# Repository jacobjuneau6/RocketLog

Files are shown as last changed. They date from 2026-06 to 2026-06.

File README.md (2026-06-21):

# RocketLog
RocketLog is a rocket altimeter designed to fit in the estes So Long rocket and provide attitude and altitude data on the rocket logging to redundant internal flash.
# Pictures
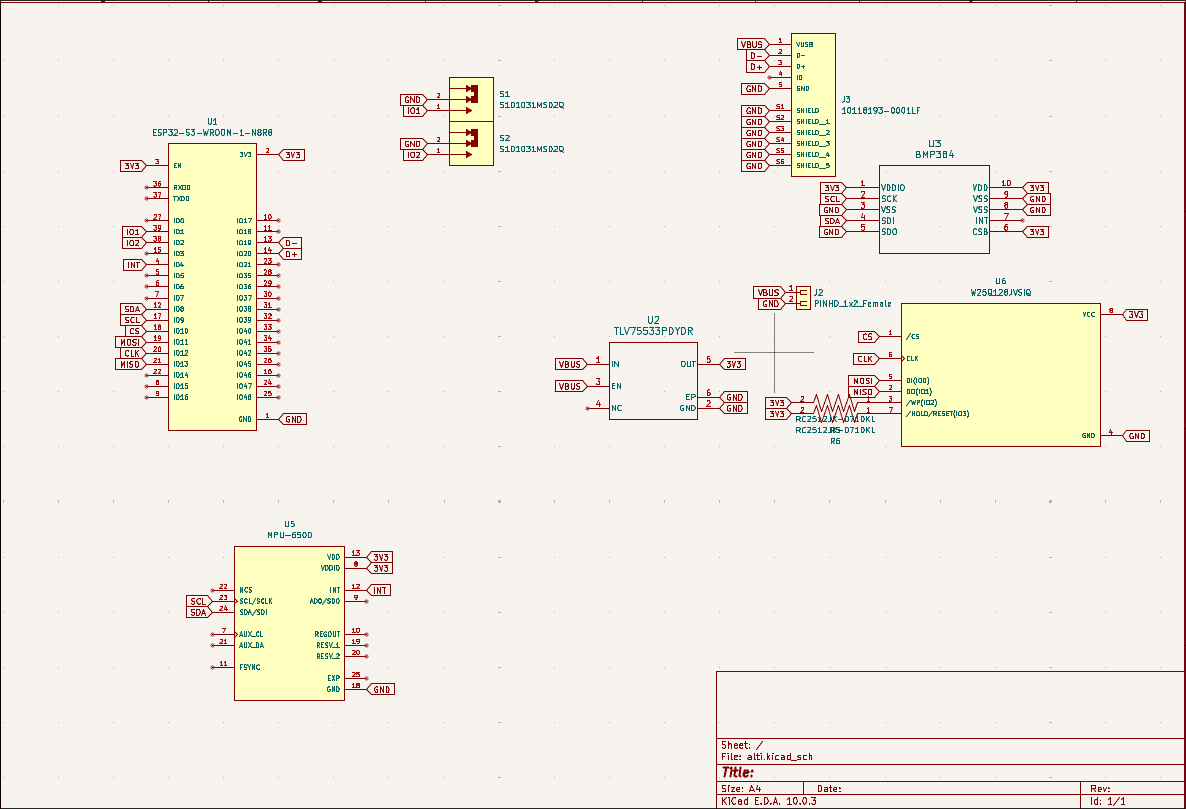
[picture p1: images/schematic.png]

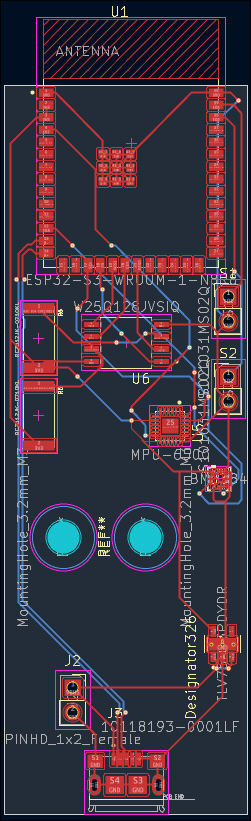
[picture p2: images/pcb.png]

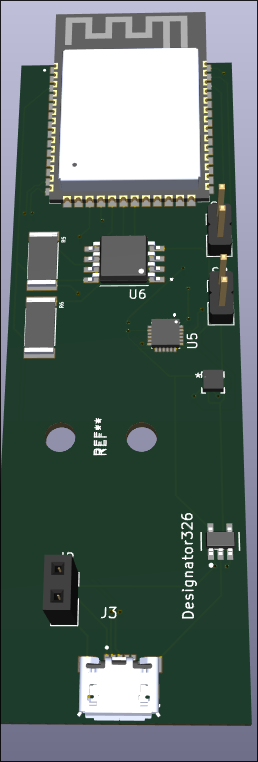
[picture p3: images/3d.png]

# Design
[![PCB Preview]()](https://kicanvas.org/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)Click the image to open the interactive KiCanvas viewer.
# Why
I have flown by custom painted and modified So Long rocket many times but have only been able to estimate the appogee and forces experienced. As I want to aluch sime more delicate payloads in the future, I want to see the forces that would be experienced by the payload before I fly some more delicate payloads.
# BOM
| Reference | Value | DigiKey_Part_Number | Link | Cost |
| --- | --- | --- | --- | --- |
| J3 | 10118193-0001LF | 609-4616-1-ND | [Link](https://www.digikey.com/en/products/detail/amphenol-cs-fci/10118193-0001LF/2785388) | $0.58 |
| R5,R6 | RC2512JK-0710KL | YAG3394CT-ND | [Link](https://www.digikey.com/en/products/detail/yageo/RC2512JK-0710KL/5922475) | $0.60 |
| U1 | ESP32-S3-WROOM-1-N8R8 | 5407-ESP32-S3-WROOM-1-N8R8CT-ND | [Link](https://www.digikey.com/en/products/detail/espressif-systems/ESP32-S3-WROOM-1-N8R8/15295891) | $6.73 |
| U2 | TLV75533PDYDR | 296-TLV75533PDYDRCT-ND | [Link](https://www.digikey.com/en/products/detail/texas-instruments/TLV75533PDYDR/22531567) | $0.30 |
| U3 | BMP384 | 828-BMP384CT-ND | [Link](https://www.digikey.com/en/products/detail/bosch-sensortec/BMP384/13681277) | $3.75 |
| U5 | MPU-6500 | 1428-1011-1-ND | [Link](https://www.digikey.com/en/products/detail/tdk-invensense/MPU-6500/4385412) | $8.00 |
| U6 | W25Q128JVSIQ | W25Q128JVSIQ-ND | [Flash](https://www.aliexpress.us/item/3256811354152848.html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) | $7.00 |
| PCB | Custom Boards & Stencils from JLCPCB | | | $27.00 |
| Battery | 300mAh battery | | [Battery](https://www.amazon.com/battery-Rechargeable-Lithium-Polymer-Connector/dp/B07BTTVX4Q?th=1) | $4.00 |
| Digikey Shipping | | | | $8.50 |

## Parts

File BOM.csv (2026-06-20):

Reference | Value | DigiKey_Part_Number
J3 | 10118193-0001LF | 609-4616-1-ND
R5,R6 | RC2512JK-0710KL | YAG3394CT-ND
U1 | ESP32-S3-WROOM-1-N8R8 | 5407-ESP32-S3-WROOM-1-N8R8CT-ND
U2 | TLV75533PDYDR | 296-TLV75533PDYDRCT-ND
U3 | BMP384 | 296-TLV75533PDYDRCT-ND
U5 | MPU-6500 | 1428-1011-1-ND
U6 | W25Q128JVSIQ | W25Q128JVSIQ-ND

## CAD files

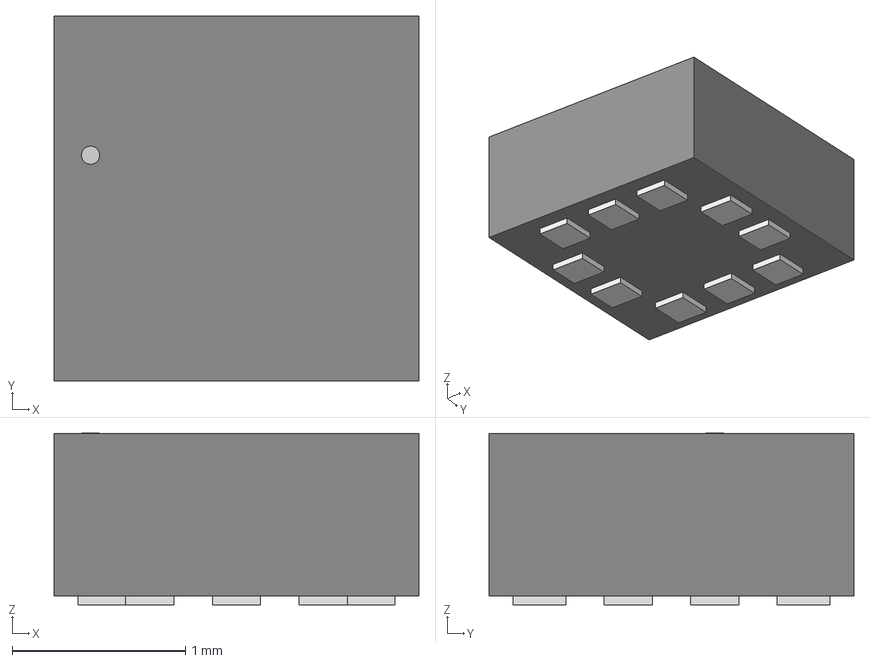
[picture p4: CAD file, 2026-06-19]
alti/symbols/BMP384/LGA10_2_0X2_0X0_95_BOS.step
2.11 x 2.11 x 0.993 mm

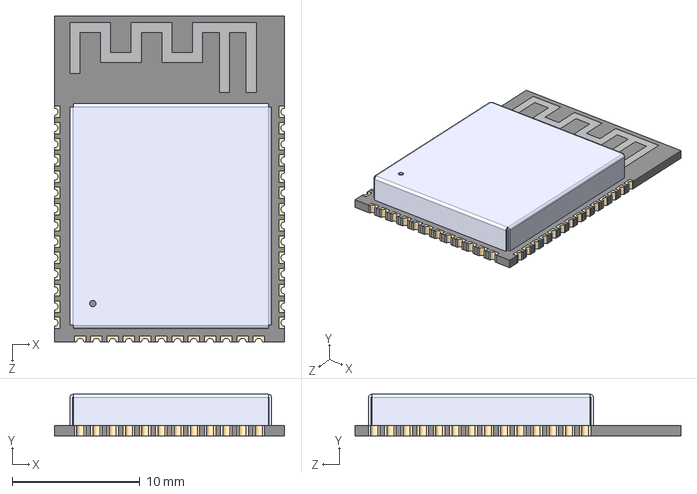
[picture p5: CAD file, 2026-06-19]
alti/symbols/ESP32-S3-WROOM-1-N8R8/ESP32-S3-WROOM-1-N8R8.step
18.0 x 3.25 x 25.5 mm

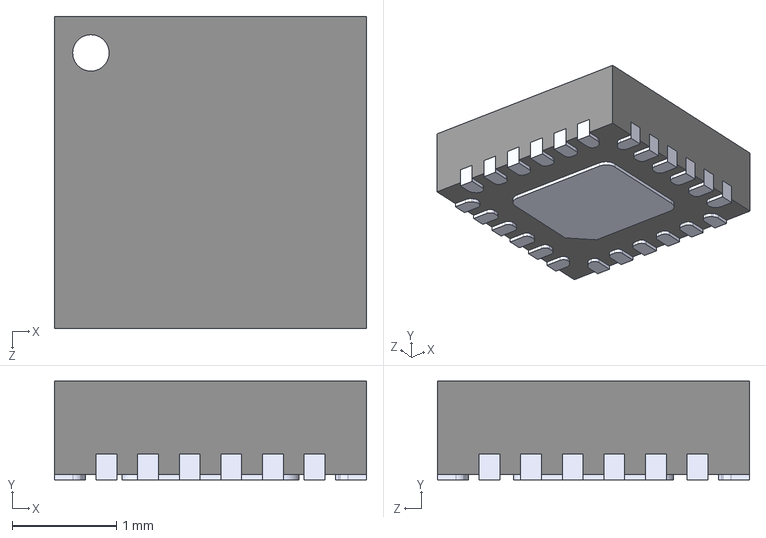
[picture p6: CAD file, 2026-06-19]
alti/symbols/MPU-6500/MPU-6500.step
3.00 x 0.95 x 3.00 mm

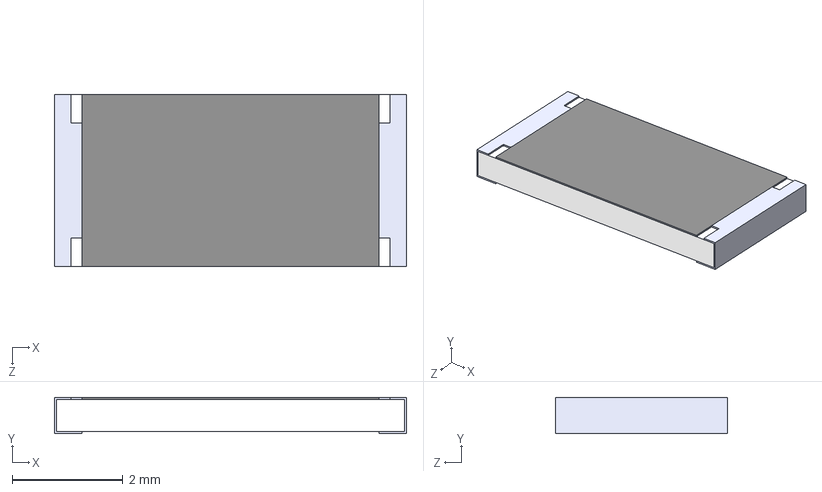
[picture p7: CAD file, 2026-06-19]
alti/symbols/RC2512JK-075K1L/RC2512JK-075K1L.step
6.35 x 0.65 x 3.10 mm

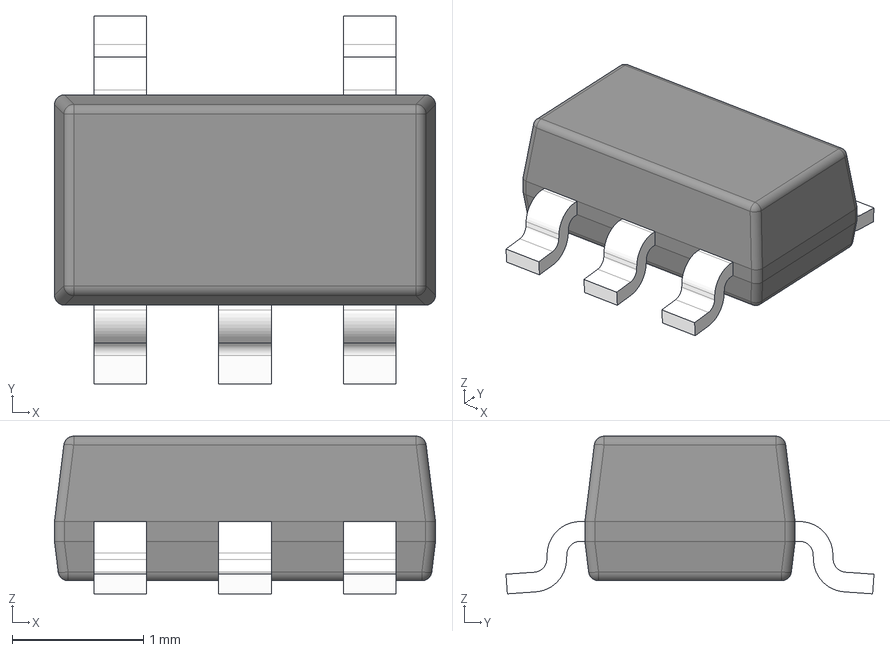
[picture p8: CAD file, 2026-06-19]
alti/symbols/ul_TLV75533PDYDR/DYD0005A.stp
2.90 x 2.80 x 1.20 mm
BODY-SOT
LEAD-SOT x 5
DIEPAD

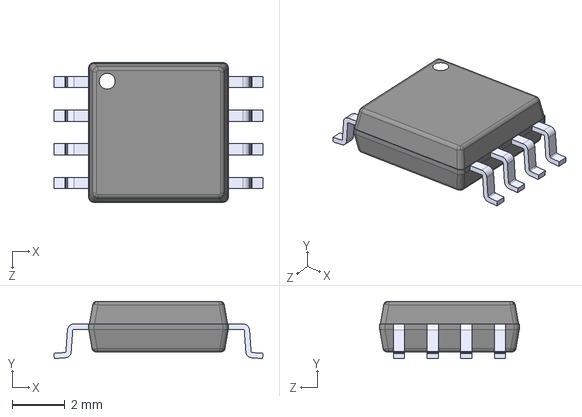
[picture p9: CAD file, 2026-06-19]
alti/symbols/W25Q128JVSIQ/W25Q128JVSIQ.step
7.90 x 2.16 x 5.28 mm

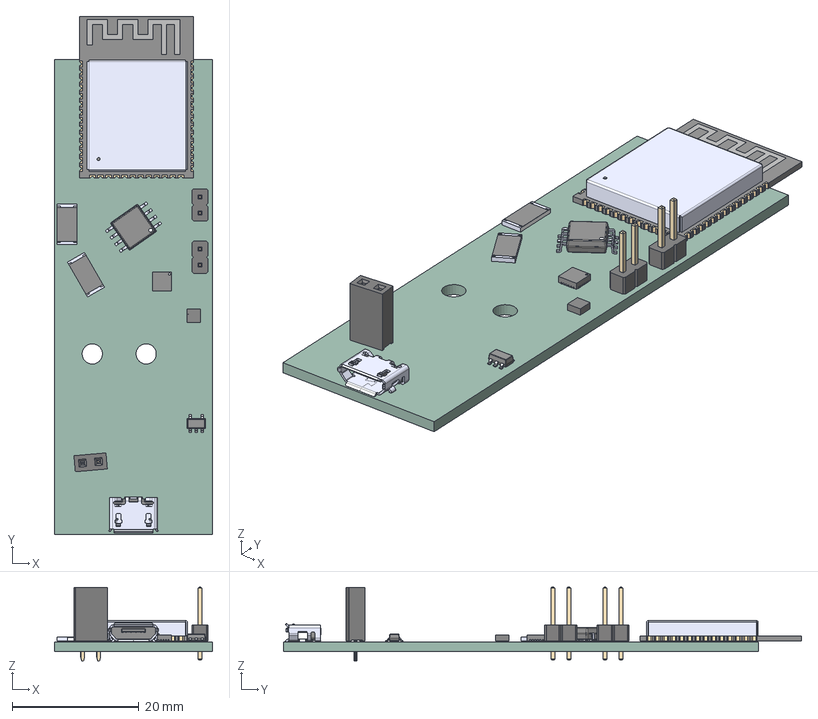
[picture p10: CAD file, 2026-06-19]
CAD/PCB.step
25.0 x 81.8 x 11.6 mm
W25Q32JWSSIQ
SR2512MK-071R1L x 2
PinHeader_1x02_P254mm_Vertical x 2
ESP32-S3-WROOM-1-N8R2
MPU-6500
10118193-0001LF
BODY-SOT
LEAD-SOT x 5
DIEPAD
PinSocket_1x02_P2.54mm_Vertical
alti_PCB

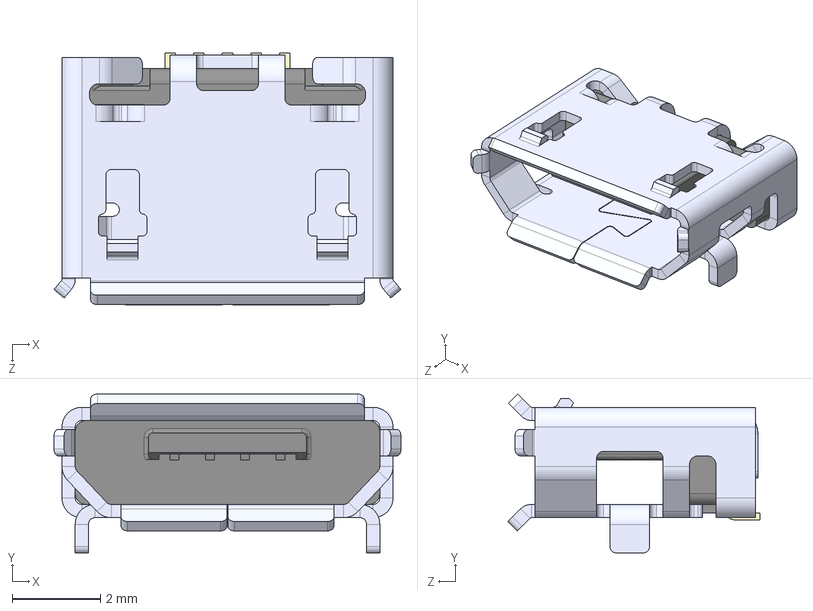
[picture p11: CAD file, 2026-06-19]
alti/symbols/10118193-0001LF--3DModel-STEP-56544.STEP
7.86 x 3.60 x 5.71 mm

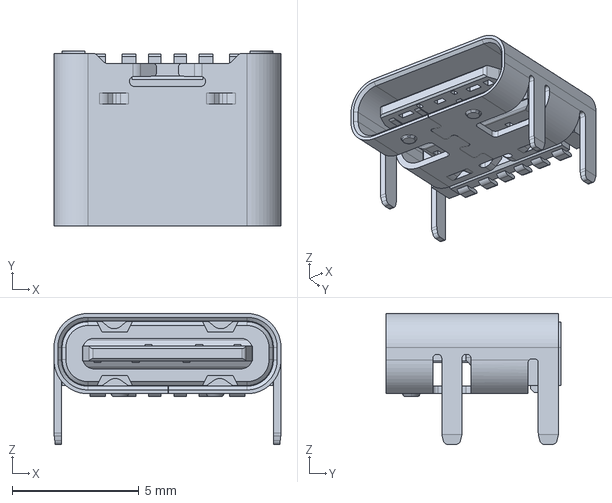
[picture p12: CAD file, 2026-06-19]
alti/symbols/2171750001/2171750001.stp
8.94 x 6.90 x 5.16 mm

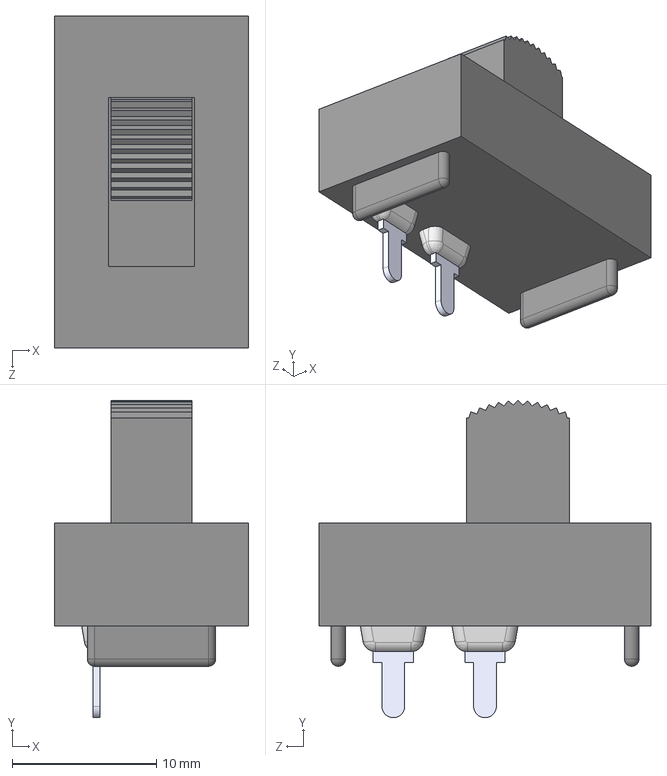
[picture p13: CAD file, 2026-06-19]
alti/symbols/S101031MS02Q/S101031MS02Q.step
13.5 x 22.0 x 23.0 mm

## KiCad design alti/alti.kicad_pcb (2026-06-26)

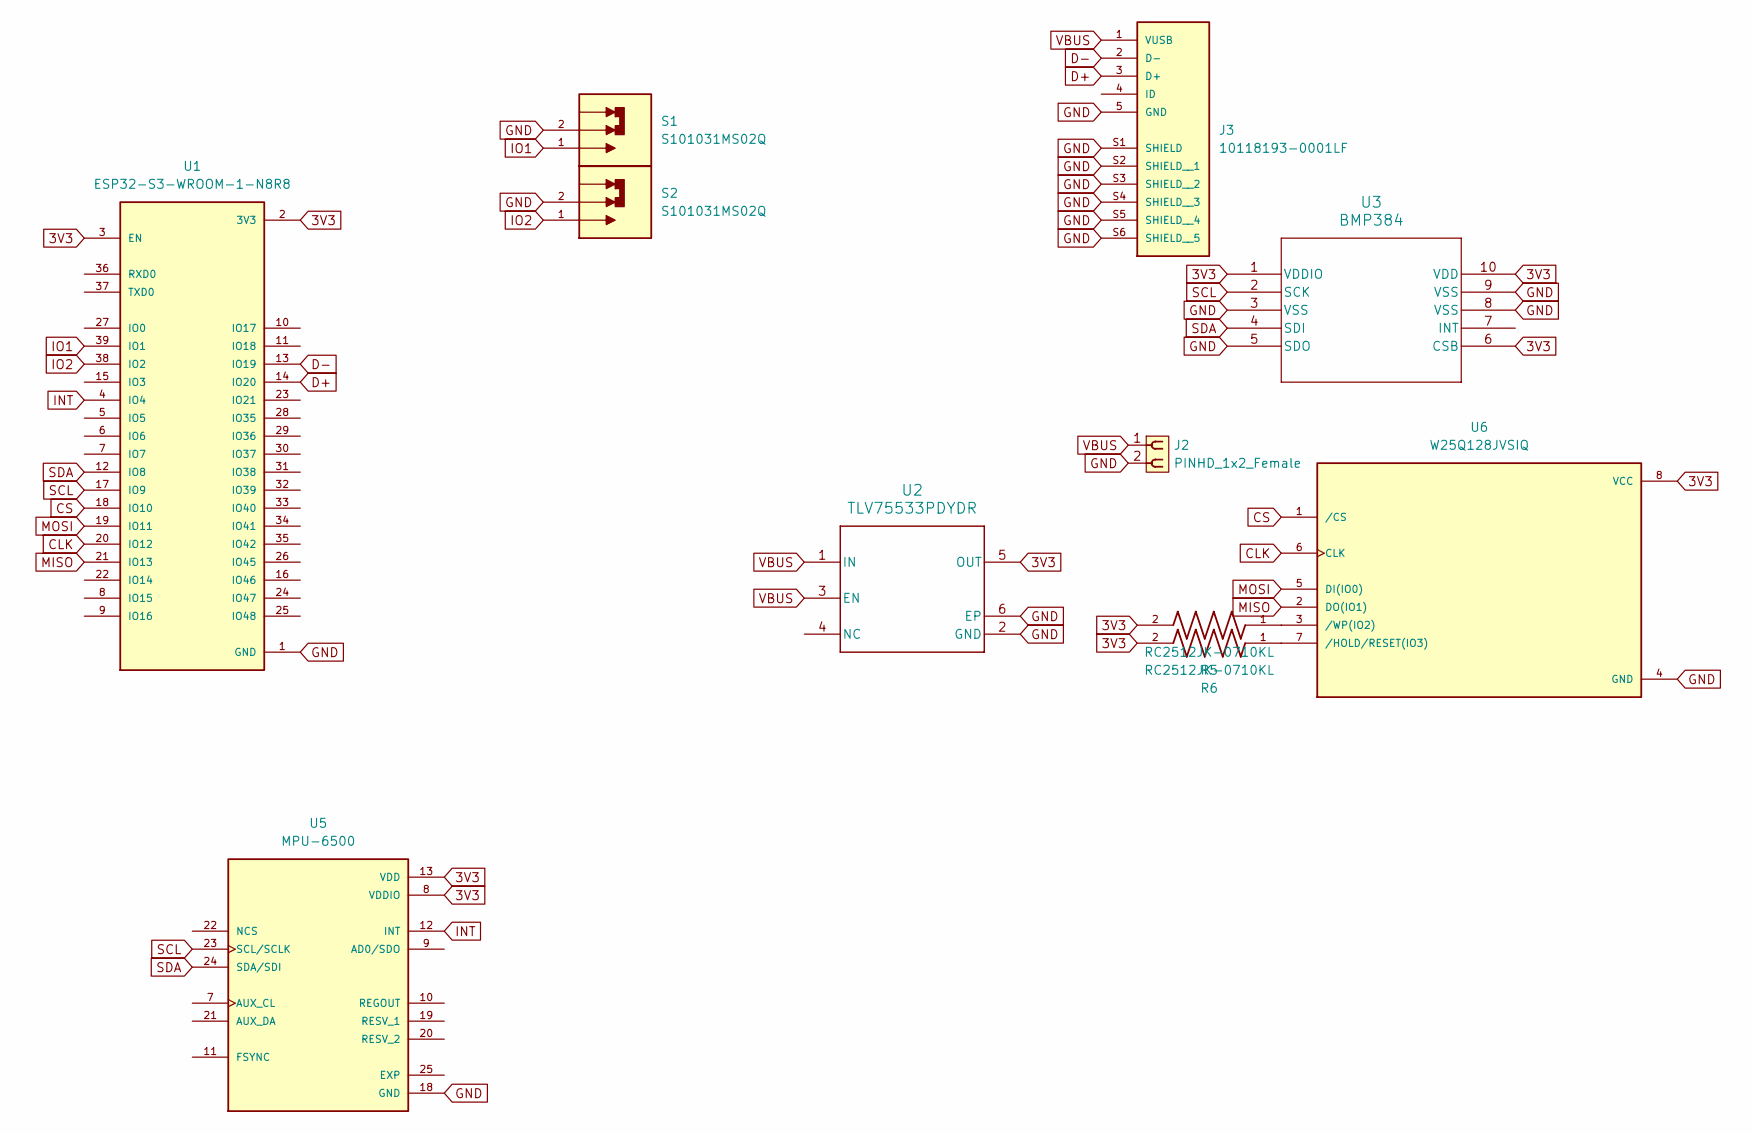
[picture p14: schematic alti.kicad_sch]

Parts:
J2: PINHD_1x2_Female; PinSocket_1x02_P2.54mm_Vertical
J3: 10118193-0001LF; AMPHENOL_10118193-0001LF; PARTREV E; DigiKey_Part_Number 609-4616-1-ND
R5, R6: RC2512JK-0710KL; RESC6331X65N; DigiKey_Part_Number YAG3394CT-ND
S1, S2: S101031MS02Q; PinHeader_1x02_P2.54mm_Vertical; PARTREV I; DigiKey_Part_Number CKN10658-ND
U1: ESP32-S3-WROOM-1-N8R8; XCVR_ESP32S3WROOM1N8R8; DigiKey_Part_Number 5407-ESP32-S3-WROOM-1-N8R8CT-ND
U2: TLV75533PDYDR; DYD0005A-MFG; DigiKey_Part_Number 296-TLV75533PDYDRCT-ND
U3: BMP384; LGA10_2.0X2.0X0.95_BOS; DigiKey_Part_Number 296-TLV75533PDYDRCT-ND
U5: MPU-6500; QFN40P300X300X95-25N; PARTREV 1.3; DigiKey_Part_Number 1428-1011-1-ND
U6: W25Q128JVSIQ; SOIC127P790X216-8N; PARTREV I; DigiKey_Part_Number W25Q128JVSIQ-ND

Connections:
3V3: R5.2, R6.2, U1.2 (3V3), U1.3 (EN), U2.5 (OUT), U3.1 (VDDIO), U3.6 (CSB), U3.10 (VDD), U5.8 (VDDIO), U5.13 (VDD), U6.8 (VCC)
CLK: U1.20 (IO12), U6.6 (CLK)
CS: U1.18 (IO10), U6.1 (/CS)
D+: J3.3 (D+), U1.14 (IO20)
D-: J3.2 (D-), U1.13 (IO19)
GND: J2.2, J3.5 (GND), J3.S1 (SHIELD), J3.S2 (SHIELD__1), J3.S3 (SHIELD__2), J3.S4 (SHIELD__3), J3.S5 (SHIELD__4), J3.S6 (SHIELD__5), S1.2, S2.2, U1.1 (GND), U1.40 (GND), U1.41_1 (GND), U1.41_2 (GND), U1.41_3 (GND), U1.41_4 (GND), U1.41_5 (GND), U1.41_6 (GND), U1.41_7 (GND), U1.41_8 (GND), U1.41_9 (GND), U2.2 (GND), U2.6 (EP), U3.3 (VSS), U3.5 (SDO), U3.8 (VSS), U3.9 (VSS), U5.18 (GND), U6.4 (GND)
INT: U1.4 (IO4), U5.12 (INT)
IO1: S1.1, U1.39 (IO1)
IO2: S2.1, U1.38 (IO2)
MISO: U1.21 (IO13), U6.2 (DO(IO1))
MOSI: U1.19 (IO11), U6.5 (DI(IO0))
unnamed: R6.1, U6.7 (/HOLD/RESET(IO3))
unnamed: R5.1, U6.3 (/WP(IO2))
SCL: U1.17 (IO9), U3.2 (SCK), U5.23 (SCL/SCLK)
SDA: U1.12 (IO8), U3.4 (SDI), U5.24 (SDA/SDI)
VBUS: J2.1, J3.1 (VUSB), U2.1 (IN), U2.3 (EN)

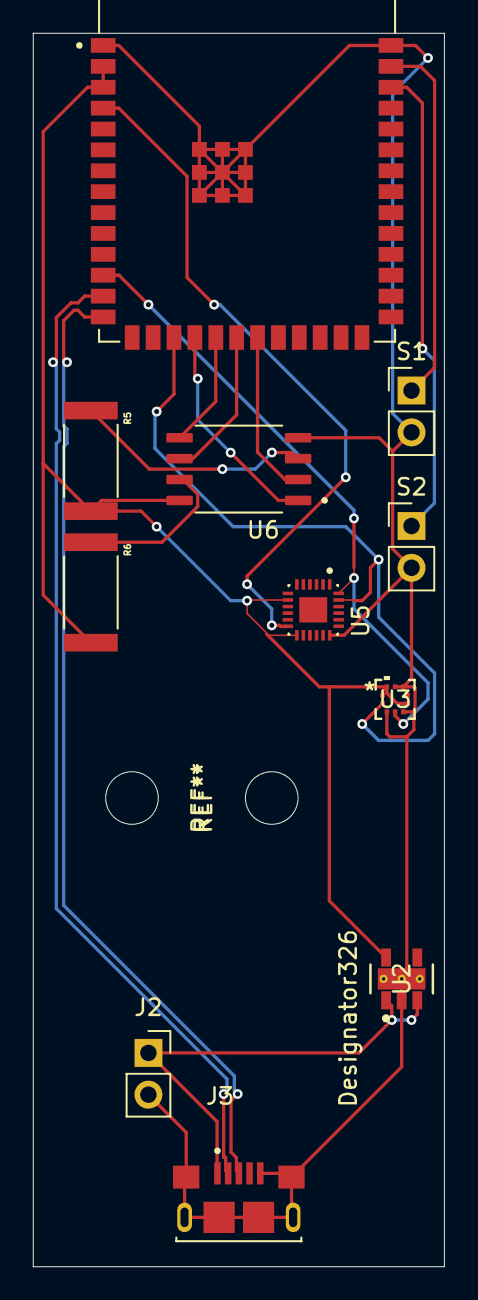
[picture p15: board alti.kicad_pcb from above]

Board: 2 copper layers, 25.0 x 75.0 mm, 11 parts (0 on the bottom side), 16 nets.

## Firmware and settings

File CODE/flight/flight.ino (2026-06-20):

#include <SPI.h>
#include <SPIMemory.h>
#include <Wire.h>
#include <Adafruit_MPU6050.h>
#include <Adafruit_BMP3XX.h>

#define FLASH_CS    10
#define SPI_MOSI    11
#define SPI_MISO    13
#define SPI_CLK     12

#define TRIG_START  1
#define TRIG_STOP   2
#define LED_PIN     21

#define I2C_SDA     8
#define I2C_SCL     9
#define MPU_INT     4

#define MPU_ADDR    0x68
#define BMP_ADDR    0x76

#define META_SECTOR 0
#define DATA_START_ADDR  4096

#define SAMPLE_RATE_US 10000
#define AUTO_STOP_MS   300000

SPIClass SPI_EXT(FSPI);
SPIFlash flash(FLASH_CS, &SPI_EXT);

Adafruit_MPU6050 mpu;
Adafruit_BMP3XX  bmp;

struct __attribute__((packed)) LogEntry {
  uint32_t timestamp;
  int16_t  accel[3];
  int16_t  gyro[3];
  float    pressure;        // Pa
  float    temperature;     // °C
};

struct __attribute__((packed)) SessionInfo {
  bool      dataValid;
  uint32_t  entryCount;
  uint32_t  crc;
};

bool loggingActive = false;
uint32_t logStartTime = 0;
uint32_t lastSampleTime = 0;
uint32_t writeAddress = DATA_START_ADDR;
uint32_t entryCount = 0;
SessionInfo meta;

void startLogging();
void stopLogging();
void logSample();
void dumpCSV();
void eraseFlashData();
void readMeta();
void writeMeta();
void printStatus();

void setup() {
  Serial.begin(115200);
  while (!Serial);

  pinMode(TRIG_START, INPUT_PULLUP);
  pinMode(TRIG_STOP,  INPUT_PULLUP);
  SPI_EXT.begin(SPI_CLK, SPI_MISO, SPI_MOSI, FLASH_CS);
  if (!flash.begin()) {
    Serial.println("Flash Init Failed.");
    while(1);
  }
  Serial.println("Flash Nominal.");
  Wire.begin(I2C_SDA, I2C_SCL);
  Wire.setClock(400000);

  if (!mpu.begin(MPU_ADDR, &Wire)) {
    Serial.println("MPU not found.");
    while(1);
  }
  mpu.setAccelerometerRange(MPU6050_RANGE_8_G);
  mpu.setGyroRange(MPU6050_RANGE_500_DEG);
  mpu.setFilterBandwidth(MPU6050_BAND_21_HZ);
  Serial.println("MPU Nominal.");

  if(!bmp.begin_I2C(BMP_ADDR, &Wire)) {
    Serial.println("BMP not found.");
    while(1);
  }
  bmp.setPressureOversampling(BMP3_OVERSAMPLING_4X);
  bmp.setTemperatureOversampling(BMP3_OVERSAMPLING_8X);
  bmp.setIIRFilterCoeff(BMP3_IIR_FILTER_COEFF_3);
  bmp.setOutputDataRate(BMP3_ODR_50_HZ);
  Serial.println("BMP Nominal.");

  readMeta();
  if (meta.dataValid && meta.entryCount > 0) {
    Serial.printf("Stored data: %u entries ready to dump. \n",meta.entryCount);
  }
  Serial.println("Ready. dump   erase   status");
}

void loop() {
  if (!loggingActive && digitalRead(TRIG_START) == HIGH) {
    delay(50);
    if (digitalRead(TRIG_START) == HIGH) {
      startLogging();
    }
  }

  if (loggingActive) {
    if (digitalRead(TRIG_STOP) == HIGH || millis() - logStartTime >= AUTO_STOP_MS) {
      delay(50);
      if (digitalRead(TRIG_STOP) == HIGH || millis() - logStartTime >= AUTO_STOP_MS) {
        stopLogging();
      }
    } else {
      uint32_t now = micros();
      if (now - lastSampleTime >= SAMPLE_RATE_US) {
        lastSampleTime = now;
        logSample();
      }
    }
  }

  if (Serial.available()) {
    String cmd = Serial.readStringUntil('\n');
    cmd.trim();
    cmd.toLowerCase();
    if (cmd == "dump") {
      if (!loggingActive) dumpCSV();
      else Serial.println("No dump during Log Session.");
    }
    else if (cmd == "erase") {
      if (!loggingActive) eraseFlashData();
      else Serial.println("No erase during Log Session.");
    }
    else if (cmd == "status") {
      printStatus();
    }
  }
}

void startLogging() {
  eraseFlashData();
  loggingActive = true;
  digitalWrite(LED_PIN, HIGH);
  logStartTime = millis();
  lastSampleTime = micros();
  writeAddress = DATA_START_ADDR;
  entryCount = 0;
  Serial.println("Logging Started Nominally.");
}

void stopLogging() {
  loggingActive = false;
  digitalWrite(LED_PIN, LOW);
  meta.dataValid = true;
  meta.entryCount = entryCount;
  writeMeta();
  Serial.printf("Logging Stopped Nominally. %u Samples were Saved. \n", entryCount);
}

void logSample() {
  sensors_event_t a, g, temp_mpu;
  mpu.getEvent(&a, &g, &temp_mpu);

  float pressure = bmp.readPressure();
  float temperature = bmp.readTemperature();
  LogEntry entry;
  entry.timestamp = millis() - logStartTime;
  entry.accel[0] = a.acceleration.x * 1000;
  entry.accel[1] = a.acceleration.y * 1000;
  entry.accel[2] = a.acceleration.z * 1000;
  entry.gyro[0] = g.gyro.x * 1000;
  entry.gyro[1] = g.gyro.y * 1000;
  entry.gyro[2] = g.gyro.z * 1000;
  entry.pressure = pressure;
  entry.temperature = temperature;

  uint8_t* p =(uint8_t*)&entry;
  for (size_t i = 0; i< sizeof(LogEntry); i++) {
    flash.writeByte(writeAddress++, p[i]);
  }

  entryCount++;
}
void dumpCSV() {
  readMeta();
  if (!meta.dataValid || meta.entryCount == 0) {
    Serial.println("No data to dump.");
    return;
  }

  Serial.println("timestamp_ms,accel_x,accel_y,accel_z,gyro_x,gyro_y,gyro_z,pressure_Pa,temperature_C");

  uint32_t addr = DATA_START_ADDR;
  LogEntry entry;

  for (uint32_t i = 0; i < meta.entryCount; i++) {
    uint8_t* p = (uint8_t*)&entry;
    for (size_t j = 0; j < sizeof(LogEntry); j++) {
      p[j] = flash.readByte(addr++);
    }

    Serial.printf("%lu,%d,%d,%d,%d,%d,%d,%.2f,%.2f\n",
      entry.timestamp,
      entry.accel[0],
      entry.accel[1],
      entry.accel[2],
      entry.gyro[0],
      entry.gyro[1],
      entry.gyro[2],
      entry.pressure,
      entry.temperature
      );
  }

  Serial.println("--- END CSV ---");
}

void readMeta() {
  uint8_t* p = (uint8_t*)&meta;
  uint32_t addr = META_SECTOR * 4096;
  for (size_t i = 0; i < sizeof(SessionInfo); i++) {
    p[i] = flash.readByte(addr++);
  }
}

void writeMeta() {
  flash.eraseSector(META_SECTOR);
  uint8_t* p = (uint8_t*)&meta;
  uint32_t addr = META_SECTOR * 4096;
  for (size_t i = 0; i < sizeof(SessionInfo); i++) {
    flash.writeByte(addr++, p[i]);
  }
}

void eraseFlashData() {
  for (uint32_t sector = 1; sector < 4096; sector++) {
    flash.eraseSector(sector);
  }
  meta.dataValid = false;
  meta.entryCount = 0;
  writeMeta();
  Serial.println("Flash data erased Nominally.");
}

void printStatus() {
  readMeta();
  Serial.printf("Logging: %s\n", loggingActive ? "ACTIVE" : "stopped");
  if (meta.dataValid) {
    Serial.printf("Stored entries: %u\n", meta.entryCount);
  } else {
    Serial.println("No stored data.");
  }
}

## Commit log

2026-06-19 add PCB
    [10118193-0001LF--3DModel-STEP-56544.STEP, 2171750001.stp, DYD0005A.stp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]
2026-06-20 Update readme with BOM info
2026-06-26 update PCB based on feedback
    [alti-B_Cu.gbr, alti-B_Mask.gbr, alti-B_Paste.gbr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]
